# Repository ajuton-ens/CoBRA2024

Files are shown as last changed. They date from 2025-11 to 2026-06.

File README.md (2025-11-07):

# CoBRA

Le projet CoBRA (Course de Ballons Réactifs et Autonomes) à pour objectif de construire un ballon dirigeable capable de suivre un parcours de façon autonome et de larguer un colis

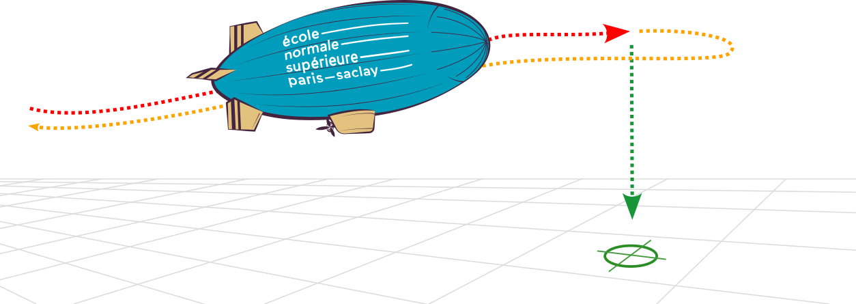
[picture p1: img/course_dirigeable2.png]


## 1 Constitution des équipes

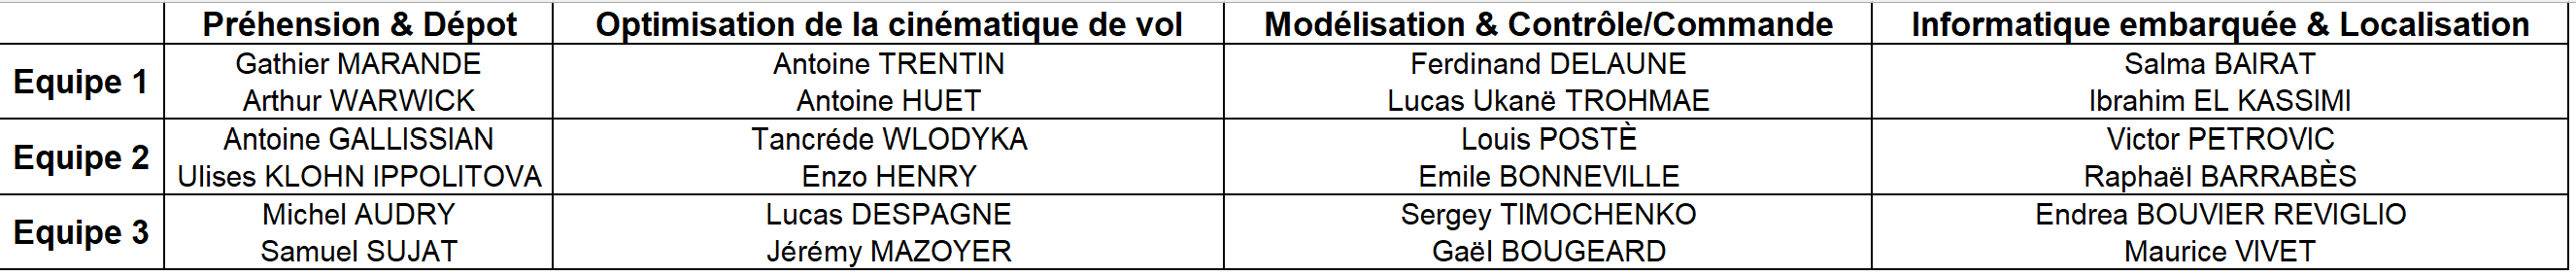
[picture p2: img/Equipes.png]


Chaque équipe doit fournir au moins 1 membre à chacun des 4 groupes de travail suivants :
* Préhension & Dépot
* Optimisation de la cinématique de vol
* Modélisation & Contrôle/Commande
* Informatique embarquée & Localisation

## 2 Analyse fonctionnelle et état de l'art
La première séance est consacrée à un travail d'étude générale du problème et d'état de l'art (projet 2023_2024 et autres dirigeables blimp).
* Découper le problème en plusieurs fonctions,
* Pour chaque fonction, spécifier les performances attendues,
* Etudier les solutions retenues en 2023 et les solutions retenues pour d'autres dirigeables,
* Etablir un schéma synoptique du dirigeable.

La semaine suivante, les groupes de travail commenceront leurs études.

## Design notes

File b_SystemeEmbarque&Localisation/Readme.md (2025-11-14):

# Systèmes embarqués et Localisation

Enseignant référent : Anthony Juton

Cette page est destinée à présenter l'avancement du travail sur :

* La prise en main de la carte Raspberry Pi Zero 2 W
* L'évaluation des télémètres infrarouge (Capteur de Distance LIDAR 8m TF-Luna)
* L'amélioration des bibliothèque d'utilisation des capteurs (BNO055, télémètre) et actionneurs (variateurs ESC et servo-moteurs)
* L'évaluation des capteurs Bosch proprioceptifs
* La localisation

## Avancement 2025-2026

**Vision**
07/11 : tests sur une nouvelle caméra des méthodes de calibration et détection des Apriltags réussis. Familiarisation avec le code de localisation utilisé actuellement sur le dirigeable. Codage sur une nouvelle camera pour la detection du centre du nouveau tag issu de la bibliothèque Aruco pour détecter le dirigeable depuis le plafond, même lorsqu'il est loin. Ceci sert pour détecter la translation du dirigeable. Pour plus tard : finalisation de ce codage pour détecter les rotations.
14/11 : Accès au stream vidéo. Début des analyses d'espacement des Apriltags.

**GPS Indoor**
GPS Indoor sous Dashboard

Tuto vidéo : https://youtu.be/Uj2_BGS1AjI 

Matériel :
- logiciel Dashboard  
-set marvelmind robotics super-MP-3D (5 beacon et un modem)

Protocole : 
1)	Installer Dashboard sur https://marvelmind.com/download/#SW ainsi que les driver nécessaire
2)	Allumer 2=ON 
3)	Connecter beacon sur le pc en filaire 
4)	Upgrade le firmware de chaque balise et du modem en haut à gauche de l’écran
5)	Cliquer sur le bouton default pour chaque beacon en bas à droite de l’écran
6)	Définir une adresse différence pour chaque beacon (ex : 1,2,3,4,5) et cliquer sur write change en haut à droite de l’écran
7)	Identifier chaque balise en mobile (Mobile Beacon a.k.a. “Hedgehog” ) ou fixe (Stationary Beacon) avec le hedgedog mode en enable ou disable . 
8)	Faire de même pour le modem (firmware+default button)
9)	Placer les balises en mesurant les distances qui les sépares et leurs altitudes respectives. 
10)	Personnellement les balises sont placées à la même hauteur (0.75 m du sol )et forme une surface rectangulaire de 3,5x5,18 m2 (voir carte associé)
11)	Créer une submap
12)	Réveiller chaque balise fixe dans la submap 0 
13)	Rentré manuellement leur position relative(x,y,z) car le mode placement auto n’est pas précis( clique droit sur le beacon sur la carte)
14)	freezsubmap 
15)	Réveiller balise mobile et fixer son altitude

=>On peut maintenant se déplacer dans l’espace (voir vidéo test)  

Piste d’amélioration :
 -placer les balises en hauteur orienté vers la zone à couvrir pour augmenter la zone et réduire les interférences du au passage des humains dans l’espace 
 
-l’altitude ne marche pas (à régler)

-position peu précise(plusieurs frezze de position) ( parfois la balise disparait) 
=>peu fiable et robuste pour le moment 
=> plus fiable/robuste avec 2 balise comme sur la vidéo tuto 

-faire un essai/test sur dirigeable en mouvement 

-intérêt pour le projet final ? 

**Proprioception**
07/11 : test du capteur BMI088, les données sont reçues via un arduino intermédiaire prochaine séance: voire à enlever l'arduino et recevoir les données directement sur le PI via I2C

## Bibliographie

[1] R. Fedorenko et V. Krukhmalev, « Indoor Autonomous Airship Control and Navigation System », MATEC Web of Conferences, vol. 42, p. 01006, 2016, doi: 10.1051/matecconf/20164201006 (http://www.matec-conferences.org/10.1051/matecconf/20164201006)

[2] J. Rao, Z. Gong, J. Luo, et S. Xie, « A flight control and navigation system of a small size unmanned airship », in IEEE International Conference Mechatronics and Automation, 2005, juill. 2005, p. 1491-1496 Vol. 3. doi: 10.1109/ICMA.2005.1626776. Disponible sur: https://ieeexplore.ieee.org/document/1626776

[3] Le site web des centrales inertielles de bosch : https://www.bosch-sensortec.com/products/motion-sensors/imus/

[8] Marvelmind propose plusieurs kits de localisation d'intérieur : https://marvelmind.com

[9] AprilTags https://april.eecs.umich.edu/software/apriltag

[10] Projet abouti https://github.com/elenagiraldo3/april_tags_autolocalization/blob/main/detect_apriltag.py

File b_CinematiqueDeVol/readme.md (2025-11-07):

# Système propulsif et directif

Enseignant référent : Bastien Durand

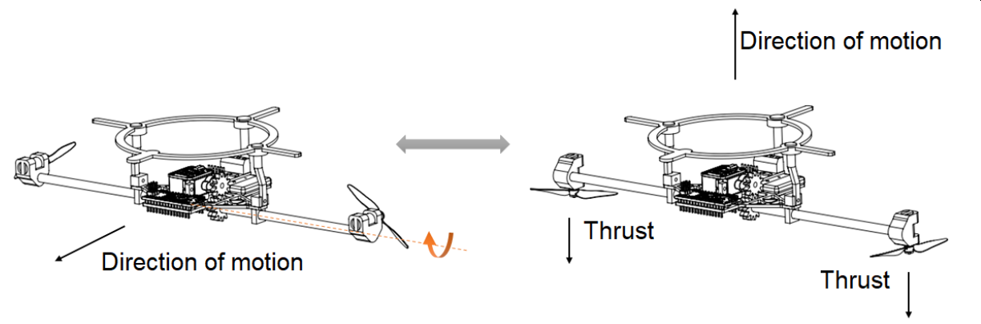
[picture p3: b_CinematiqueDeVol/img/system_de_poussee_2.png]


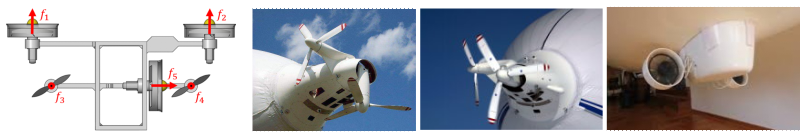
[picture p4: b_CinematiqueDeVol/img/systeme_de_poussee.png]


**Objectif** : proposer et comparer plusieurs systèmes pour déplacer et diriger le ballon (critère de comparaison, masse embarquée, consommation d'énergie, contrôlabilité, ...)

## Bibliographie

[1] J. R. H. Carvalho et al., « System Architecture of a Robotics Airship », in Proceedings of IDEAS 2019, L. Pereira, J. R. H. Carvalho, P. Krus, M. Klofsten, et V. J. De Negri, Éd., in Smart Innovation, Systems and Technologies. Cham: Springer International Publishing, 2021, p. 13‑22. doi: 10.1007/978-3-030-55374-6_2 [(paper)](./bibliographie/Carvalho et al. - 2021 - System Architecture of a Robotics Airship.pdf)

[2] F. Repoulias et E. Papadopoulos, « Dynamically feasible trajectory and open-loop control design for unmanned airships », in 2007 Mediterranean Conference on Control & Automation, juin 2007, p. 1‑6. doi: 10.1109/MED.2007.4433820. Disponible sur: https://ieeexplore.ieee.org/document/4433820

[3] S. Ul Ferdous, A. Mohammadi, et S. Lakshmanan, « Developing a low-cost autonomous blimp with a reduced number of actuators », in Unmanned Systems Technology XXI, C. M. Shoemaker, P. L. Muench, et H. G. Nguyen, Éd., Baltimore, United States: SPIE, mai 2019, p. 13. doi: 10.1117/12.2519252. Disponible sur: https://www.spiedigitallibrary.org/conference-proceedings-of-spie/11021/2519252/Developing-a-low-cost-autonomous-blimp-with-a-reduced-number/10.1117/12.2519252.full

[4] Y. Wen, L. Chen, Y. Wang, D. Sun, D. Duan, et J. Liu, « Nonlinear DOB-based explicit NMPC for station-keeping of a multi-vectored propeller airship with thrust saturation », The Aeronautical Journal, vol. 122, nᵒ 1257, p. 1753‑1774, nov. 2018, doi: 10.1017/aer.2018.91 (https://www.cambridge.org/core/journals/aeronautical-journal/article/abs/nonlinear-dobbased-explicit-nmpc-for-stationkeeping-of-a-multivectored-propeller-airship-wit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)

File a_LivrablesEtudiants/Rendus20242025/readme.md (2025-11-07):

# Info 2024/25

Pour désactiver la sortie 5 volts de la carte Raspberry pi 5

Ouvrir le fichier config.txt: sudo nano /boot/firmware/config.txt

Ajouter la igne suivante :
PSU_MAX_CURRENT=5000

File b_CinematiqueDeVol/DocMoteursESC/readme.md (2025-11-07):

# Composants

## Composants de la solution constructeur, le [Ballon de 2m de chez Aero Drum Ltd](https://www.rc-zeppelin.com/fr/int%C3%A9rieur-rc-blimps-2m.html)

| | |
| --- | --- |
|  | Moteur hélice<br />KAVAN Brushless motor [C2822-1200](https://www.kavanrc.com/en/item/kavan-brushless-motor-c2822-1200-140792)<br />Kv = 1200 rpm/V<br />Alim Lixx 2-3S<br />Diamètre axe 3.175 mm <br />Poids: 34 g|
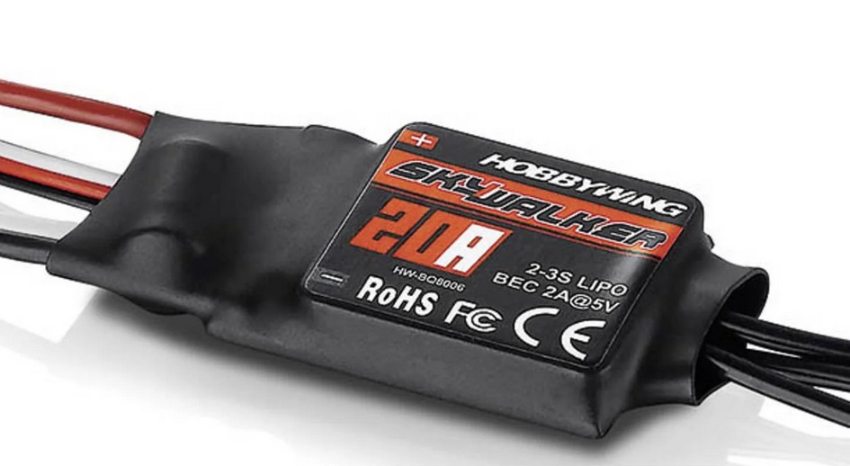
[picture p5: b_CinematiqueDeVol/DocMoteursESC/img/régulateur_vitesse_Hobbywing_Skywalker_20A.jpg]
|  | Régulateur pour moteur brushless<br />Hobbywing Skywalker 20A [Manuel](./hobbywing-skywalker-20a-regulateur-brushless-mode-demploi.pdf)<br />BEC 5V/2A<br />Alim LiPo 2-3S<br />Dimension 48x22,5 x 6 mm<br />Poids: 16,5 g|
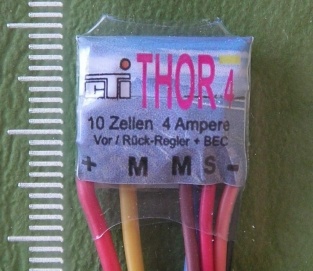
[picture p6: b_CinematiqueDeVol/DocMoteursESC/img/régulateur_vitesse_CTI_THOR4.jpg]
|  | Régulateur pour MCC deux sens de marche<br />CTI [Thor 4](https://www.cti-modellbau.de/-74-102-110-161.html) <br />Taille: 16 x 13 x 4 mmm<br />|
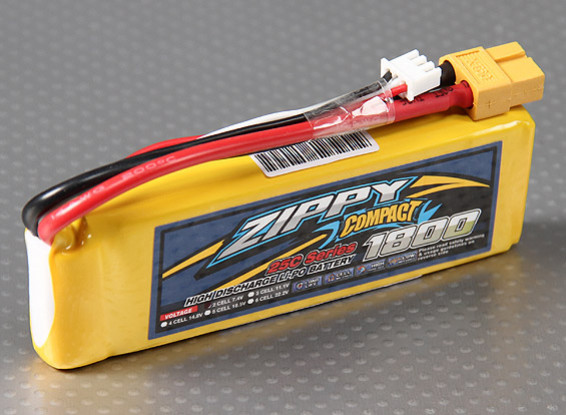
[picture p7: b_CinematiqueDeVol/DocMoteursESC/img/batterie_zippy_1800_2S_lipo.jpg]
| | Batterie<br />[Zippy compact 1800mAh 2S 25C Lipo](https://hobbyking.com/fr_fr/zippy-compact-1800mah-2s-25c-lipo-pack.html)<br />Voltage: 2S1P / 2 cellules / 7.4V<br />Poids: 110g<br />Dimensions: 105x34x16mm<br />Solde Fiche: JST-XH<br />Fiche de décharge: XT60 |
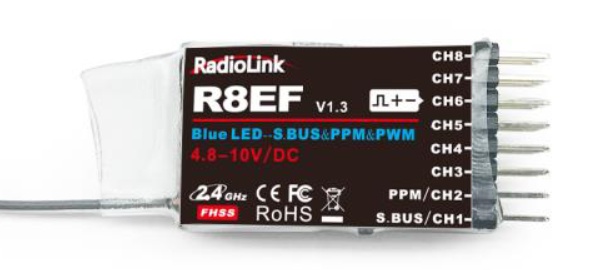
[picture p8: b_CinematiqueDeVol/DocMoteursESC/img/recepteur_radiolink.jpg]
|  | Récepteur radio<br />[Radiolink R8EF, 2.4G 8 channels receive](https://www.radiolink.com/r8ef)<br />[manuel](./Radiolink_R8EF+Introduction+Manul_2021.8.3.pdf)<br />Poids: 7g<br />Taille: 41.5 x 21.5 x 11.5mm |
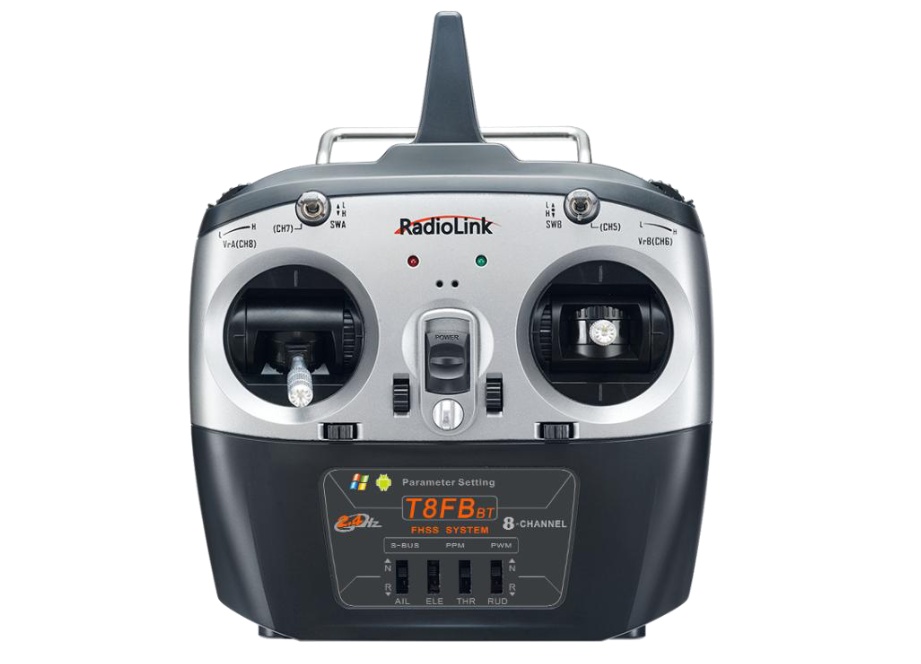
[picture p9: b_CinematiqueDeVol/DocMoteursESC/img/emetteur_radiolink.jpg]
|  | Emetteur radio<br />[Radiolink T8EF(TB), 2.4G 8 channels receive](https://www.radiolink.com/r8ef)<br />[manuel](./Radiolink_T8FB(BT)+User+Manual(with+R8EF+receiver)+2023.9.14.pdf), [Logiciels](https://www.radiolink.com/t8fb_bt_app)

## Composants pour défi 2024

| | |
| --- | --- |
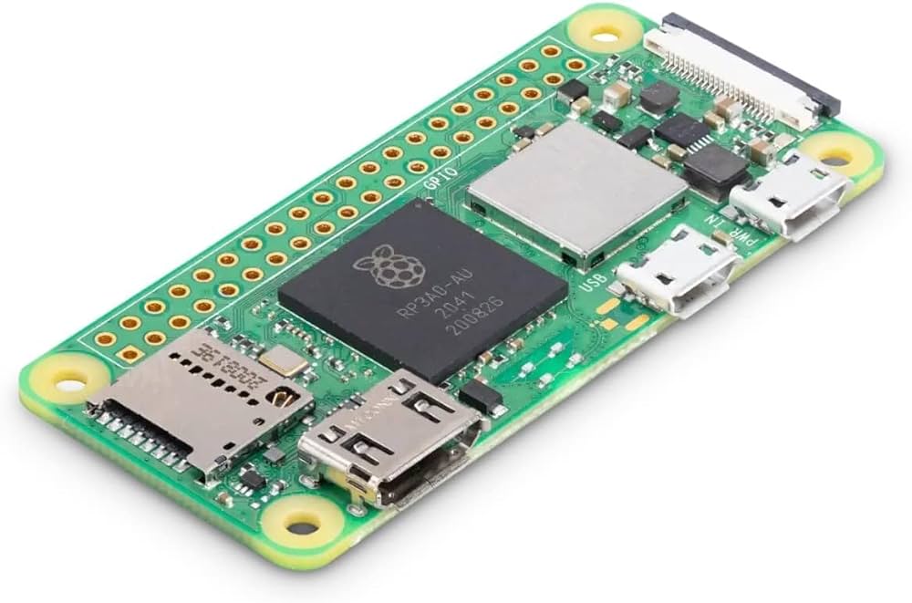
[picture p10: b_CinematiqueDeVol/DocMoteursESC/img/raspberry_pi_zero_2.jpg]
| |Contrôler - Raspberry Pi Zero 2 W<br />[schéma électrique](https://datasheets.raspberrypi.com/rpizero2/raspberry-pi-zero-2-w-reduced-schematics.pdf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..)<br />[plan mécanique](https://datasheets.raspberrypi.com/rpizero2/raspberry-pi-zero-2-w-mechanical-drawing.pdf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..)<br />[Documentation](https://www.raspberrypi.com/documentation/)|
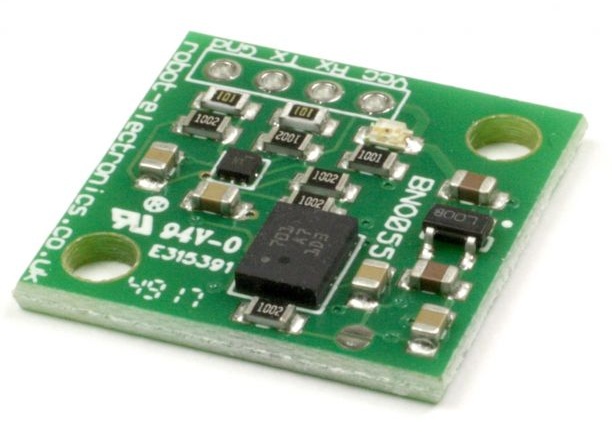
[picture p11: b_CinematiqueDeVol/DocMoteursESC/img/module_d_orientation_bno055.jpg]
|  | Module orientation absolue 9 DOF<br />[Robot electronics BNO 055](https://www.robot-electronics.co.uk/products/sensors/compass-sensors/bno055.html)<br />[Datasheet](./BNO055_datasheet.pdf), [Schéma](./BNO055_datasheet.pdf), [Layout](./BNO055_layout.pdf) BME680|
||Capteur environnemental<br />[SparkFun Environmental Sensor Breakout - BME680](https://www.sparkfun.com/products/16466) |
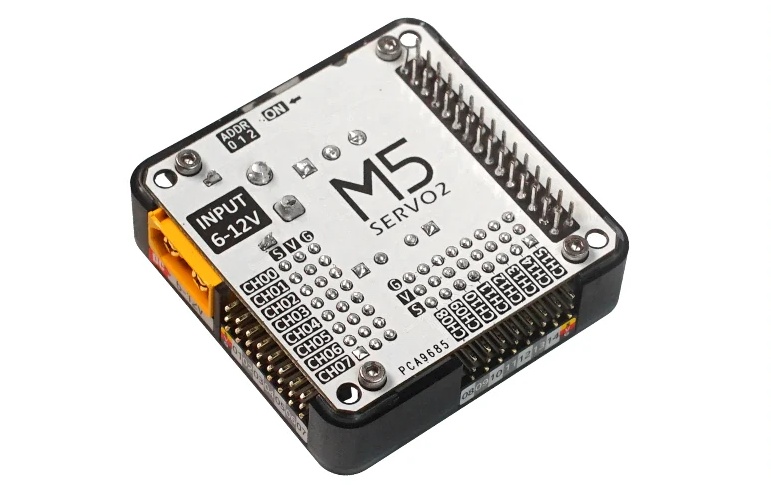
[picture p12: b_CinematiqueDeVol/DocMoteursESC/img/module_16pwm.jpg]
| | Module servo 16 canaux<br> M5Stack [ SERVO2 Module 16 Channels - 13.2 (PCA9685)](https://shop.m5stack.com/products/servo2-module-16-channels-13-2-pca9685) |
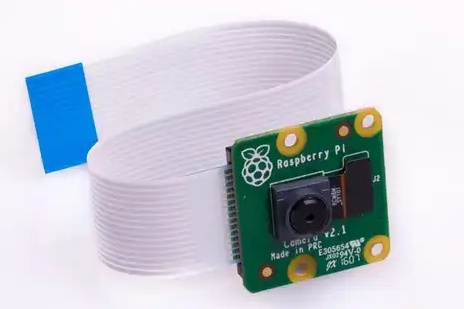
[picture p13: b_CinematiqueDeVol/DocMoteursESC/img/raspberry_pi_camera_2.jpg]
||Raspberry Pi [Camera Module 2](https://www.raspberrypi.com/products/camera-module-v2/)|
|  | Moteur brushless pour hélice<br />[Pichler Pulsar Shocky Pro 2204](https://shop.pichler.de/Brushless-Motor-PULSAR-Shocky-Pro-2204-1400-KV_1) |
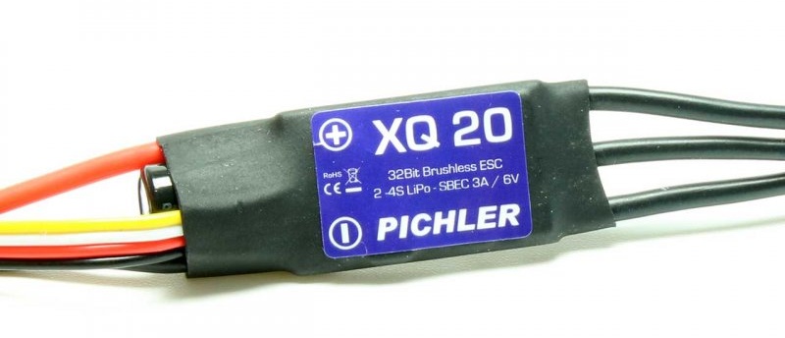
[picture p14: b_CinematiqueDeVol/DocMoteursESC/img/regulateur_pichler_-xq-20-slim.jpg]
|  | Régulateur brushless pour moteur hélice <br />[Pichler XQ+ 20 Slim](https://shop.pichler.de/Brushless-Speed-Controller-ESC-XQ-20-Slim)<br />[manuel](./pichler-xq-20-slim_manuel.pdf) |
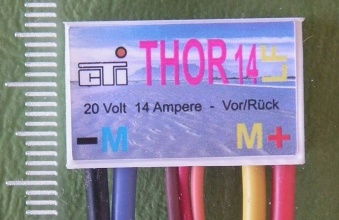
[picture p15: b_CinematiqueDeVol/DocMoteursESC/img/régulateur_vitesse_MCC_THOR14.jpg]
| | Régulateur pour MCC deux sens de marche<br />CTI [Thor 14](https://www.cti-modellbau.de/-150-151-152-166.html) |
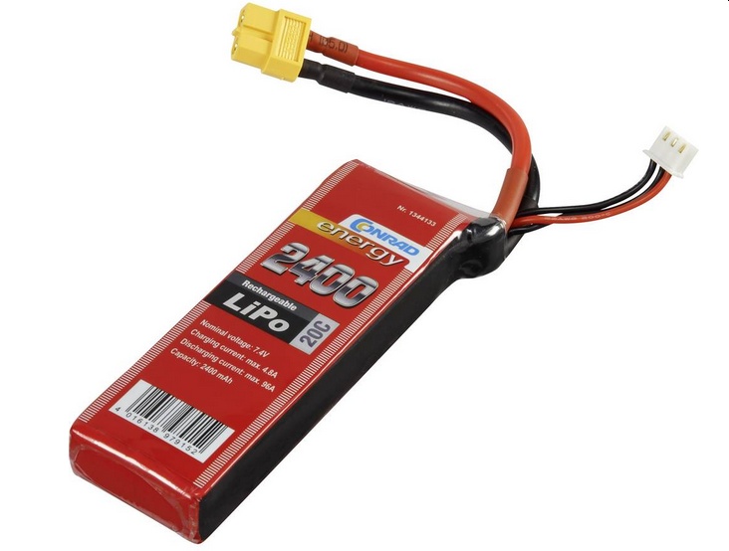
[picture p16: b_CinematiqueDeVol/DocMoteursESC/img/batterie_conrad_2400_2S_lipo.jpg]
| | Batterie<br />[Conrad 2400mAh 2S 20C Lipo](https://www.conrad.fr/fr/p/pack-de-batterie-lipo-7-4-v-2400-mah-conrad-energy-1344133-20-c-softcase-xt60-1344133.html)<br />Voltage: 2S1P / 2 cellules / 7.4V<br />Poids: 143g<br />Dimensions: 112x35x19mm<br />Connecteur: XH<br />Raccordement: XT60 |

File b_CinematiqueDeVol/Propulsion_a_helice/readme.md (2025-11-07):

# Propulsion à hélice

Enseignant référent : Bruce Anglade

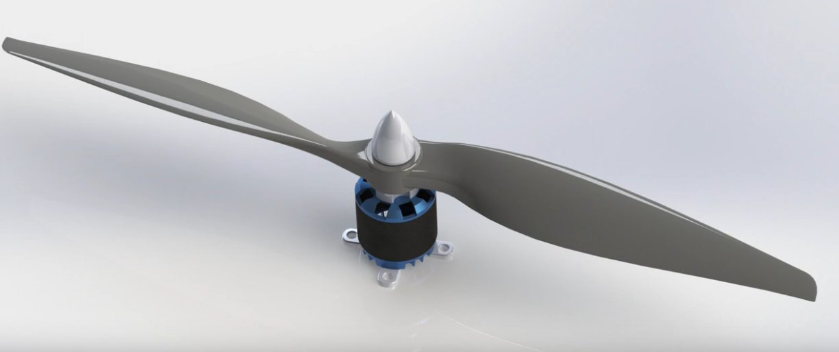
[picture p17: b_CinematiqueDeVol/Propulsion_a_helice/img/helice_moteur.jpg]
hélice + moteur


Étudiants (4) :

- Nicolas Detzen - nicolas.detzen@ens-paris-saclay.fr
- Louis Amitrano - louis.amitrano@ens-paris-saclay.fr
- Ulysse Poulain - ulysse.poulain@ens-paris-saclay.fr
- Ahmed Nachawati- ahmed.nachawati@ens-paris-saclay.fr

**objectif** : étudier la relation entre l'effort de poussée et le signal de commande, la masse totale (hélice, moteur, esc), la consommation électrique.

## Bibliographie

[1] Blimp Drone Thruster Design Overview, (23 juillet 2019). Disponible sur: https://www.youtube.com/watch?v=tUxTVcdhqJs

[2] N. Landell-Mills, Propeller thrust explained by Newtonian physics. 2021. Disponible sur: https://www.researchgate.net/publication/350604844_Propeller_thrust_explained_by_Newtonian_physics

[3] Comment savoir si son moteur et son hélice feront voler l’avion RC, (17 juillet 2022). Disponible sur: https://www.youtube.com/watch?v=99sh-BjobWw

[4] « Aircraft Propeller Theory », AeroToolbox, 24 avril 2020. Disponible sur: https://aerotoolbox.com/propeller/

[5] « Théorie de la quantité de mouvement », Wikipédia. 30 juin 2023. Disponible sur: https://fr.wikipedia.org/w/index.php?title=Th%C3%A9orie_de_la_quantit%C3%A9_de_mouvement&oldid=205599257

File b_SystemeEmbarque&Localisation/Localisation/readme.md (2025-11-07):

# Localisation d'intérieur

**Objectif** : évaluer et comparer des techniques de localisation en intérieur (ex:  radiogoniométrie Bluetooth, capteur de flux optique, fingerprinting, triangulation par vision, centrale inertielle...)

**Matériel disponible** : 
* des cartes microcontrôleurs Microbit programmables en python (avec récepteur bluetooth), des cartes microcontrôleur STM32 programmables en C, des raspberry Pi et raspberry Pi zéro (Wifi + bluetooth)
* des caméras RPI 2
* des capteurs de pression bme280
* des centrales inertielles avec Motion Processor Unit BNO055 et des centrales MPU9250
* tous les détecteurs de présence bluetooth de l'école et toutes les bornes wifi
* un kit MarvelMind Starter set Super-MP [8]

## Vision SLAM

*Mathis Goupillon* et *Guillian Audry* ont installé {Ubuntu 22.04 ; ROS2 Humble} sur une RPI4. Ils s'intéressent maintenant à la mise en oeuvre des 3 noeuds : 

* acquisition de l'image de la caméra (caméra RPI ou caméra USB)
* acquisition des données de la centrale inertielle (IMU)
* mise en oeuvre du noeud SLAM pour obtenir la carte et la position sur la carte.

Si tout fonctionne bien, il est envisageable sans trop de difficulté avec ROS2 de délocaliser le noeud SLAM sur un PC fixe, les noeuds acquisition image et IMU restant évidemment dans le contrôleur embarqué dans le dirigeable.

## Vision apriltag

*Mathieu Guerin* et *Maxime Degraeve* ont installé Raspberry OS sur une RPI zéro. L'acquisition de l'image d'une caméra USB est opérationnel. Ils ont commencé à installer apriltag pour la reconnaissance des tags (QR Code grossiers) et le calcul de leur position et orientation. Avec la position de 1 ou plusieurs tags (placés précisément dans l'atrium) dans le repère du dirigeable, on peut retrouver la position du dirigeable dans l'atrium.
L'utilisation de la smart-caméra HuskyLens est laissée de côté pour l'instant, ayant trop peu de possibilités de réglage.

## Radio

*Simon Chardin*, *Pierre-Louis Filoche* et *Pierrot Cadeilhan* ont travaillé sur le fingerprint. Après quelques essais et de la lecture biblio, la solution semble, comme on pouvait s'y attendre, peu précise (2,6 m annonce la biblio). Elle est donc abandonnée.
En attendant l'évaluation d'un système Marvelmind au retour des vacances, les étudiants ont travaillé sur micro:bit à la mise en oeuvre de télémètre ultrason SRF02 et SRF10 pour la détection d'obstacle.

## Proprioception
*Damien Chevalier* met en oeuvre sur micro:bit le capteur BME280 (température, pression, humidité) et fait une recherche de capteurs de pression plus précis. *Mathias Le Maigat* met en oeuvre la centrale inertielle (IMU) BNO055 pour estimer d'abord l'orientation du dirigeable (roll, pitch, yaw) et si possible pour estimer la position relative à la position de départ.

## Bibliographie

[1] Ellisys Bluetooth Video #14: Bluetooth Direction Finding, (8 mai 2019). Disponible sur: https://www.youtube.com/watch?v=38O2aK-aiaw

[2] R. Fedorenko et V. Krukhmalev, « Indoor Autonomous Airship Control and Navigation System », MATEC Web of Conferences, vol. 42, p. 01006, 2016, doi: 10.1051/matecconf/20164201006 (http://www.matec-conferences.org/10.1051/matecconf/20164201006)

[3] J. Rao, Z. Gong, J. Luo, et S. Xie, « A flight control and navigation system of a small size unmanned airship », in IEEE International Conference Mechatronics and Automation, 2005, juill. 2005, p. 1491-1496 Vol. 3. doi: 10.1109/ICMA.2005.1626776. Disponible sur: https://ieeexplore.ieee.org/document/1626776

[4] S. Subedi et J.-Y. Pyun, « Practical Fingerprinting Localization for Indoor Positioning System by Using Beacons », Journal of Sensors, vol. 2017, p. e9742170, déc. 2017, doi: 10.1155/2017/9742170 (https://www.hindawi.com/journals/js/2017/9742170/)

[5] X. Yu, H. Wang, et J. Wu, « A method of fingerprint indoor localization based on received signal strength difference by using compressive sensing », EURASIP Journal on Wireless Communications and Networking, vol. 2020, nᵒ 1, p. 72, avr. 2020, doi: 10.1186/s13638-020-01683-8 (https://doi.org/10.1186/s13638-020-01683-8)

[6] Angle of Arrival - Bluetooth 5.1 Direction Finding Explanation, (28 janvier 2019). Disponible sur: https://www.youtube.com/watch?v=c3XqbEKmNcM

[7] « Optical flow », Wikipedia. Disponible sur: https://en.wikipedia.org/w/index.php?title=Optical_flow&oldid=1152281324

[8] Marvelmind propose plusieurs kits de localisation d'intérieur : https://marvelmind.com

[9] AprilTags https://april.eecs.umich.edu/software/apriltag

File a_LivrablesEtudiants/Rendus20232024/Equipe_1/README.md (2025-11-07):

# Equipe n°1
## Régulateur de tension : I50115H
Droite : sortie (5V)    
Milieu : GND     
Gauche : entrée (7-36V)     
(on regarde du coté de l'étiquette-coil les pins vers le bas)

## Raspberry pi 02:
[Pinout](https://www.etechnophiles.com/rpi-zero-2w-board-layout-pinout-specs-price/)

## What i did in pip (venv/Team1) :
   
pip install adafruit-circuitpython-servokit     
pip install smbus        
pip install gpiozero        
pip install pigpio       
pip install numpy                  
pip install adafruit_bno055                  
pip install adafruit_circuitpython_bno055                  
pip install micropython_machine                  
pip install pycryptodome                  
pip install matplotlib                  

## To launch a python script in a venv:
Activate the venv : source venv/.../bin/activate         
sudo venv/.../bin/python ...py

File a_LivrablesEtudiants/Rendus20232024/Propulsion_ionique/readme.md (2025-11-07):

# Propulsion ionique

Enseignant référent : Fabien Adam

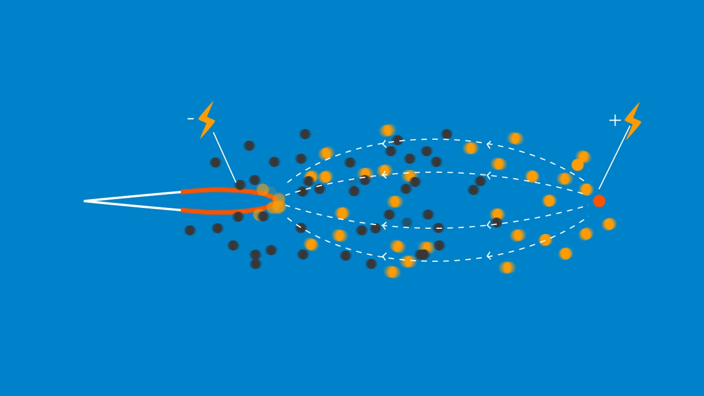
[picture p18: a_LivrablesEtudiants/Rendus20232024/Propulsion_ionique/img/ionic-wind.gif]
principe


Étudiants (4) :

- Chemsdine Ahmidach
- Melchior Personnaz
- Eliot Morard
- Samuel Dahan
- Gatien Séguy

**objectif** : élaborer un prototype et identifié l'effort de poussée obtenue en fonction du des paramètres géométriques, des matériaux et de la tension d'alimentation.

## Bibliographie

[1] S. Bernard et J.-L. Naudin, « Le projet Blimp-Lifter ». Disponible sur: http://lifterproject.online.fr/blimplifter/index.htm

[2] Ion Thruster (Side), (29 juillet 2021). Disponible sur: https://www.youtube.com/watch?v=zYVo_XjFou4

[3] Ionocraft flying, (30 août 2015). Disponible sur: https://www.youtube.com/watch?v=7nM2u2FDWsQ

[4] Electroaerodynamic Propulsion:  Is it viable?, (28 novembre 2022). Disponible sur: https://www.youtube.com/watch?v=YaLEClKGnXc

[5] C. K. Gilmore, « Electro-aerodynamic thrust for fixed-wing aircraft propulsion », Thesis, Massachusetts Institute of Technology, 2017. Disponible sur: 
https://dspace.mit.edu/handle/1721.1/112452

[6] N. Gomez-Vega, H. Xu, J. M. Abel, et S. R. H. Barrett, « Performance of decoupled electroaerodynamic thrusters », Applied Physics Letters, vol. 118, nᵒ 7, p. 074101, févr. 2021, doi: 10.1063/5.0038208

[7] Overview of MIT’s solid-state airplane, (22 novembre 2018). Disponible sur: https://www.youtube.com/watch?v=TeJyMbSSUIc

[8] J.-L. Naudin, « The Lifters Experiments ». Disponible sur: http://jnaudin.free.fr/lifters/main.htm

[9] « MIT engineers fly first-ever plane with no moving parts », MIT News | Massachusetts Institute of Technology, 21 novembre 2018. Disponible sur: https://news.mit.edu/2018/first-ionic-wind-plane-no-moving-parts-1121

[10] « Effet Biefeld-Brown », Wikipédia. 21 avril 2023. Disponible sur: https://fr.wikipedia.org/w/index.php?title=Effet_Biefeld-Brown

Ajouts des étudiants :

[11] « Force on an Asymmetric Capacitor », Thomas B. Bahder.,  Christian Fazi, ARMY RESEARCH LAB ADELPHI MD (2003), Disponible sur https://apps.dtic.mil/sti/pdfs/ADA416740.pdf

[12] Condensateur constitué par deux cylindres conducteurs: http://gerald.philippe.free.fr/files/2011/Conducteurs%20cylindriques%20en%20electrostatique.pdf
                   
[12 bis] https://claude-gimenes.fr/physique/charges-electriques/electrostatique/-iii-conducteurs-caracteristiques-principales
[13] https://arxiv.org/ftp/arxiv/papers/2002/2002.11662.pdf

[14] lien excel des mesures de la manipulation : https://ensparissaclayfr-my.sharepoint.com/:x:/g/personal/eliot_morard_ens-paris-saclay_fr/EfxHjnEue7dDnhFTeHGlXIUB3nb06A8fXRtblNC-Fcx1Bg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

[15] lien excel du planning prévisionnel : https://1drv.ms/x/s!AoqnbC4eiIVSijU25wS_YBNnT-w0

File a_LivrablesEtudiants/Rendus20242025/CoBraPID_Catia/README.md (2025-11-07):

# Remarques sur le contenu de ce dossier

Globalement, j'y ai mis les principaux fichiers nécessaires pour faire la propulsion du dirigeable. Certains manquent, comme le fichier Eagle de la carte électronique et le schéma de branchement, mais sont déjà sur le GitHub. J'ai tout modélisé sur Fusion360 donc j'ai mis les fichiers mais j'imagine que vous ne les utiliserez pas. Je n'ai mis que les fichiers aboutis, sauf le fichier principal du programme python qui fait fonctionner le dirigeable : c'est Victor qui a l'intégralité des dépendances et bibliothèques qu'il a utilisées/crées sur ROS2 sur une carte TF donc je n'ai mis que ma version de travail du programme ("main version de travail.py"). 

Vous y trouverez :

- **Le dossier "Impression"** qui contient uniquement et intégralement les fichiers stl de la structure. Quelques remarques et pistes d'amélioration :
  - "Supports moteurs bas rework.stl" est de mauvaise conception : l'hélice est trop proche de l'enveloppe et l'effet de peau fait que l'hélice aspire même en soufflant dans le bon sens. Sinon la structure est robuste et très très légère. J'ai modélisé une version améliorée mais je ne l'ai pas imprimée et donc pas testée...
  - "Supports moteurs bas.stl" est correct mais légèrement fragile selon moi et nécessiterait de mettre un cercle autour des hélices pour protéger l'utilisateur
  - "support pi cam inclinée.stl" n'a finalement pas été  utilisé puisque nous avons choisi de ne pas mettre de caméra inclinée (il était prévu d'en mettre une avec un angle de 35°)
- **Les dossiers "catia treuil AG" et "pince"** contiennent les fichiers CATIA des pièces pour la pince et le treuil. Ces pièces ont été modélisées par Ulises et Antoine Gallissian
- J'ai fourni notre poster qui contient quelques schémas et des indications utiles
- "cobra_TFLUNA_v03.py" est une version de test fonctionnelle du TFLUNA. La fonction peut être implémentée telle quelle
- "main version travail.py" : comme je disais, j'avais fait une copie du programme qui tourne pendant le fonctionnement du ballon pour travailler dessus avant d'effectuer les modifications dans le code de la raspberry (pour travailler chez moi et à cause des limites du tunnel ssh). C'est donc une version temporaire qui ne fonctionne pas forcément (je ne me souviens plus) mais qui donne 99% du fonctionnement global de la boucle 
- J'ai inclus aussi le dessin technique de la caméra raspberry utilisée (afin de la modéliser sur le fichier 3D) et la "documentation" (très incomplète et imprécise) du driver du moteur brushless.

Amusez-vous bien sur le meilleur projet de Saphire ! 😀

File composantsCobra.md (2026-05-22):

#Composants du dirigeable CoBRA

convertisseur dc-dc

Carte rasberry: PI 5

Camera : -module 3 wide (embarquée)
         -Svpro  SV-USBGS1200P01-H120 (stationnaire)

Moteurs : AS2303 F3P / 3D / 4D 2300KV 17GR T-MOTOR Intermodel 13,75 €
https://www.intermodel.fr/moteurs-electriques/12387-as2303-f3p-3d-4d-2300kv-17gr-t-motor-t-motor-brushless-moteur-3d-f3p-2300kv-4d-t-motor-as2303.html

ESC : CONTROLEUR 16A F3P 3D/4D T-MOTOR Intermodel 24,90 €
https://www.intermodel.fr/controleurs-bec/12179-controleur-16a-f3p-3d4d-t-hobby-t-motor-controleur-3d-f3p-4d-16a.html

Carte de commande :Grove PCA9685 (bus i2c vers PWM pour ESC)

Hélices : APC LP05050E 5x5E Speed 400 Electric Conrad 2,74€
https://www.conrad.fr/fr/p/apc-propeller-electrique-helice-d-avion-5-x-5-pouces-12-7-x-12-7-cm-lp05050e-2139530.html

LiDAR : TF-Luna
https://files.seeedstudio.com/wiki/Grove-TF_Mini_LiDAR/res/SJ-PM-TF-Luna-A03-Product-Manual.pdf

Accéléromètre : Grove BMI088

Capteur de pression : Adafruit LPS22

magnétometre :BMM350 

batterie : https://www.conrad.fr/fr/p/reely-pack-de-batterie-lipo-7-4-v-2400-mah-nombre-de-cellules-2-20-c-softcase-xt60-2617748.html

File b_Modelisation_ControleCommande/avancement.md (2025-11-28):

# Avancement de la modélisation et du contrôle

En octobre, prise en main du dirigeable, essais de réglage du correcteur de l'axe z.

Bilan ?

Quels programmes sont fonctionnels ?

Novembre : 
Séance du 7 novembre

PID_eloi : stable mais non précis -> erreur de 5cm pour 2m
Première approche des April Tags : grande liste convient , vibration du moteur pour vitesse > 25 : tags non détecté
Erreur de minimum : 2 minimums détectés -> lié au calcul de position 

Essai en XY (code essai..._dg , fichier: 10:24) : commande avant : gauche positif, droit négatif
Bascule et chute en commande avant-arrière

Travail sur lacet : sens horaire : 4 moteurs en positif

Séance 14 novembre
PID :

PID_alt = PID(30, 0, 1e6, 40, 0.1, 0.00001)
PID_lacet = PID(2, 0, 1e4, 30, 0.05, 0.0001)

28 novembre :

Changement pin moteur : pin 3 -> zg et pin 6 -> zd 
test_lib v12

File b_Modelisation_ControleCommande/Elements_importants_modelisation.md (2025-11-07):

## Paramètres ballons

1. Poids : $3kg$
2. Lift capacity : $0.3kg$
3. Volume : $3m^3$
4. Diamètre : $1.5m$
5. Longueur : $2m$

## Centre de poussé + centre des masses :

- doivent être à la verticale l'un de l'autre
- centre de masse de la nacelle doit être immobile (rotation des éléments autour de C.d.G)

## Frottements fluides 

3 formes de frottement en fonction du nombre de Reynolds:
1. $R_e < 1 : \quad$  $F_f = -3 \pi\mu D\cdot V$
1. $30 < R_e < 80 : \quad$  $F_f$ prop. a $V^{1.4}$ 
1. $R_e > 1 : \quad$ $F_f = -\frac{1}{2}\cdot \rho S C_x\cdot V^2$

[Source](https://fr.wikipedia.org/wiki/Frottement_fluide)

## Application numérique 
$R_e = \rho \frac{d_{cara}}{\mu}\cdot V $

Pour de l'air à faible vitesse : $\rho = 1 kg/m^3$ et $V = 1m/s $

Table : $\mu = 2e-5$

[Diamètre caractéristique](https://www.rc-zeppelin.com/indoor-rc-blimps-2m.html) : $d_{cara} = 1.5 m$

$R_e \sim 150\ 000$

Tables

## Drag coefficient
Streamline body : $C_x = 0.04$ ??

[Tableau](https://www.engineeringtoolbox.com/drag-coefficient-d_627.html), 
[wiki](https://en.wikipedia.org/wiki/Drag_coefficient) 

A voir

## Bilan des forces 
- Poids (en G)
- Poussée d'archimède (en P)
- Propulsion (en A) 
- Force de frottements fluides (en B)
- Forces des ailettes (horizontales et verticales)

... à compléter

Source pour bilan des forces : https://www.planete-sciences.org/espace/IMG/pdf/airships.pdf

## Poids et forces des hélice/moteurs

Moteurs moyen : $4.6N$ et $110g$

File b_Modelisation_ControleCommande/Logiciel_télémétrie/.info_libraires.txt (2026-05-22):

Le fichier point d'entrée du programme est : main.py

Liste des librairies utilisées :
  - time
  - math
  - tkinter
  - json
  - threading
  - socket
  - matplotlib
  - collections

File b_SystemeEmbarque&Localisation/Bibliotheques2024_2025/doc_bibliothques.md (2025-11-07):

# documentation des bibliothèques 2025

## bibliothèque bno055

### fonction initialisation

### fonction calibration

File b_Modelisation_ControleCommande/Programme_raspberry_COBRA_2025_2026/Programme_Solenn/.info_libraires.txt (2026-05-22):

Le fichier point d'entrée du programme est : aserv_h_2025_solenn.py

Liste des librairies externes utilisées :
  librairies par défault sur python :
  - time
  - math
  - os
  - json
  - numpy
  - threading
  - socket
  
  librairies à installer :
  - smbus2
  - cv2
  - picamera2
  - apriltags
  - gpiozero

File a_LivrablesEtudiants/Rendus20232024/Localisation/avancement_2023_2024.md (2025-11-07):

# Avancement du travail sur la localisation

connexions sur Covapsy2
192.168.50.130 cobrapi4

## Ven. 13/10/2023
### SLAM: *Guillan* + *Mathis*
  - lire rapports *Thomas*/*Kévin* (ROS2)
  - expliquer ROS2
  - installer ROS2
### AprilTag: *Maxime* et *Mathieu*
  - lire AprilTag
  - imprimer tags
  - installer caméra
  - installer bibliothèque sur RPI
  (si trop lent en local on peut streamer les données)
### Bilan quantitatif de l'essai boussole: *Damien* et *Mathias*
  - récupérer le bilan quantitatif des essais boussole
  - lire les infos des capteurs BME280, BNO055
  - biblio sur les nouveaux capteurs
  - ultrasons pour la détection d'obstacles
### Fingerprint: *Simon*, *Pierre-Louis* et *Pierrot*
  - essai dans l'atrium avec 2 emetteurs (checker erreur relatives)
  - essai de mesure de puissance bluetooth et WiFi avec ESP32 (c ou micropython)
  - lire doc marvelMind

# Localisation d'intérieur

**Objectif** : évaluer et comparer des techniques de localisation en intérieur (ex:  radiogoniométrie Bluetooth, capteur de flux optique, fingerprinting, triangulation par vision, centrale inertielle...)

**Matériel disponible** : 
* des cartes microcontrôleurs Microbit programmables en python (avec récepteur bluetooth), des cartes microcontrôleur STM32 programmables en C, des raspberry Pi et raspberry Pi zéro (Wifi + bluetooth)
* des caméras RPI 2
* des capteurs de pression bme280
* des centrales inertielles avec Motion Processor Unit BNO055 et des centrales MPU9250
* tous les détecteurs de présence bluetooth de l'école et toutes les bornes wifi
* un kit MarvelMind Starter set Super-MP [8]

## Vision SLAM

*Mathis Goupillon* et *Guillian Audry* ont installé {Ubuntu 22.04 ; ROS2 Humble} sur une RPI4. Ils s'intéressent maintenant à la mise en oeuvre des 3 noeuds : 

* acquisition de l'image de la caméra (caméra RPI ou caméra USB)
* acquisition des données de la centrale inertielle (IMU)
* mise en oeuvre du noeud SLAM pour obtenir la carte et la position sur la carte.

Si tout fonctionne bien, il est envisageable sans trop de difficulté avec ROS2 de délocaliser le noeud SLAM sur un PC fixe, les noeuds acquisition image et IMU restant évidemment dans le contrôleur embarqué dans le dirigeable.

## Vision apriltag

*Mathieu Guerin* et *Maxime Degraeve* ont installé Raspberry OS sur une RPI zéro. L'acquisition de l'image d'une caméra USB est opérationnel. Ils ont commencé à installer apriltag pour la reconnaissance des tags (QR Code grossiers) et le calcul de leur position et orientation. Avec la position de 1 ou plusieurs tags (placés précisément dans l'atrium) dans le repère du dirigeable, on peut retrouver la position du dirigeable dans l'atrium.
L'utilisation de la smart-caméra HuskyLens est laissée de côté pour l'instant, ayant trop peu de possibilités de réglage.

## Radio

*Simon Chardin*, *Pierre-Louis Filoche* et *Pierrot Cadeilhan* ont travaillé sur le fingerprint. Après quelques essais et de la lecture biblio, la solution semble, comme on pouvait s'y attendre, peu précise (2,6 m annonce la biblio). Elle est donc abandonnée.
En attendant l'évaluation d'un système Marvelmind au retour des vacances, les étudiants ont travaillé sur micro:bit à la mise en oeuvre de télémètre ultrason SRF02 et SRF10 pour la détection d'obstacle.

## Proprioception
*Damien Chevalier* met en oeuvre sur micro:bit le capteur BME280 (température, pression, humidité) et fait une recherche de capteurs de pression plus précis. *Mathias Le Maigat* met en oeuvre la centrale inertielle (IMU) BNO055 pour estimer d'abord l'orientation du dirigeable (roll, pitch, yaw) et si possible pour estimer la position relative à la position de départ.

## Bibliographie

[1] Ellisys Bluetooth Video #14: Bluetooth Direction Finding, (8 mai 2019). Disponible sur: https://www.youtube.com/watch?v=38O2aK-aiaw

[2] R. Fedorenko et V. Krukhmalev, « Indoor Autonomous Airship Control and Navigation System », MATEC Web of Conferences, vol. 42, p. 01006, 2016, doi: 10.1051/matecconf/20164201006 (http://www.matec-conferences.org/10.1051/matecconf/20164201006)

[3] J. Rao, Z. Gong, J. Luo, et S. Xie, « A flight control and navigation system of a small size unmanned airship », in IEEE International Conference Mechatronics and Automation, 2005, juill. 2005, p. 1491-1496 Vol. 3. doi: 10.1109/ICMA.2005.1626776. Disponible sur: https://ieeexplore.ieee.org/document/1626776

[4] S. Subedi et J.-Y. Pyun, « Practical Fingerprinting Localization for Indoor Positioning System by Using Beacons », Journal of Sensors, vol. 2017, p. e9742170, déc. 2017, doi: 10.1155/2017/9742170 (https://www.hindawi.com/journals/js/2017/9742170/)

[5] X. Yu, H. Wang, et J. Wu, « A method of fingerprint indoor localization based on received signal strength difference by using compressive sensing », EURASIP Journal on Wireless Communications and Networking, vol. 2020, nᵒ 1, p. 72, avr. 2020, doi: 10.1186/s13638-020-01683-8 (https://doi.org/10.1186/s13638-020-01683-8)

[6] Angle of Arrival - Bluetooth 5.1 Direction Finding Explanation, (28 janvier 2019). Disponible sur: https://www.youtube.com/watch?v=c3XqbEKmNcM

[7] « Optical flow », Wikipedia. Disponible sur: https://en.wikipedia.org/w/index.php?title=Optical_flow&oldid=1152281324

[8] Marvelmind propose plusieurs kits de localisation d'intérieur : https://marvelmind.com

[9] AprilTags https://april.eecs.umich.edu/software/apriltag

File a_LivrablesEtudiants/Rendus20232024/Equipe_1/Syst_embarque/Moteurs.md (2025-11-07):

# Documentation de l'équipe 1 pour l'utilisation des moteurs

## Servo-moteurs

Un servo moteur est défini par plusieurs paramètres :
- angles : `[angle_max, angle_repos, angle_min]`
- les instructions PWM associées  : `[pwm_max, pwm_repos, pwm_min]`
- le channel de connection : `int : c`

Attention : l'index  de la position `1` sur les boards est souvent le channel `0` !!

On définit plusieurs fonctions pour le servo :
#### `calculate_imp(angle)`

Permet de calculer la largeur d'impulsion à envoyer pour atteindre la position demandée. Les valeurs limites `angle_max` et `angle_min` entrées lors de la définition servent de bornes pour éviter d'abimer le servo.

#### `set_angle(angle)`

Permet d'envoyer la commande pwm au servo via le channel associé.
Une conversion liée à la bibliothèque `adafruit_servokit` est alors nécessaire.

## Moteurs brushless

Un moteur brushless est défini par plusieurs paramètres :
- les instructions PWM associées aux vitesses max et min  : `[pwm_max, pwm_min]`
- le channel de connection : `int : c`

Le moteur est commandé en vitesse entre `0` (min) et `1` (max).
Les valeurs de pwm calculées seront comprises entre 1000 µs et 2000 µs.

#### `initialisation()`

Il est nécessaire d'initialiser les ESC au démarrage. On envoit donc pendant quelques secondes une commande d'impulsion nulle (`pwm = 1000`). Le delay n'est pas placé dans cette fonction mais doit être pris en compte dans le script global.

#### `calculate_imp(speed)`

Permet de calculer la largeur d'impulsion à envoyer pour atteindre la vitesse demandée. Les valeurs limites `0` et `1`servent de bornes pour éviter d'abimer le moteur ou l'ESC.

#### `set_speed(speed)`

Permet d'envoyer la commande pwm à l'ESC via le channel associé.
Une conversion liée à la bibliothèque `adafruit_servokit` est alors nécessaire.

## Machine à courant continue

La MCC possède 2 sens de rotation et est commandée comme un moteur brushless. Il y a donc 2 plages de valeurs à définir :
- sens positif : `forward` entre `0` et `1`
- sens invers : `backward` entre `0` et `-1`

Une MCC est défini par plusieurs paramètres :
- les instructions PWM associées aux vitesses max et min  : `[pwm_max_forw, pwm_min_forw, pwm_min_back, pwm_max_back]`
- le channel de connection : `int : c`

Les plages de valeurs en pwm seront comprises entre 1000 µs et 2000 µs et une zone morte est construite dans l'ESC commandant la MCC autour de 1550 µs.

Le moteur est commandé en vitesse entre `0` (min) et `1` (max).

#### `initialisation()`

Il est nécessaire d'initialiser les ESC au démarrage. On envoit donc pendant quelques secondes une commande d'impulsion nulle (`pwm = 1550` pour la MCC). Le delay n'est pas placé dans cette fonction mais doit être pris en compte dans le script global.

#### `calculate_imp(speed)`

Permet de calculer la largeur d'impulsion à envoyer pour atteindre la vitesse demandée. Les valeurs limites `0`, `1` et `-1` servent de bornes pour éviter d'abimer le moteur ou l'ESC.

#### `set_speed(speed)`

Permet d'envoyer la commande pwm à l'ESC via le channel associé.
Une conversion liée à la bibliothèque `adafruit_servokit` est alors nécessaire.

#### `stop()`

Envoit comme consigne la valeur `pwm = 1550` pour un arrêt du moteur (zone morte de l'ESC).

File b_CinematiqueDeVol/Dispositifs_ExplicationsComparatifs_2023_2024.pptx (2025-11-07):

## CoBra

- Système propulsif et directif -

BOURDIOT Mathys
COULSON Jérémy
MPACKO PRISO Fantine
RAPAILLE Quentin
RETAILLEAU Mathieu

1/ Etablissement d’un cahier des charges
2/Propositions de dispositions de moteurs
3/ Nécessité et choix des matériaux
4/ Servomoteur
5/ Bilan

## 1/ Diagramme d’exigences

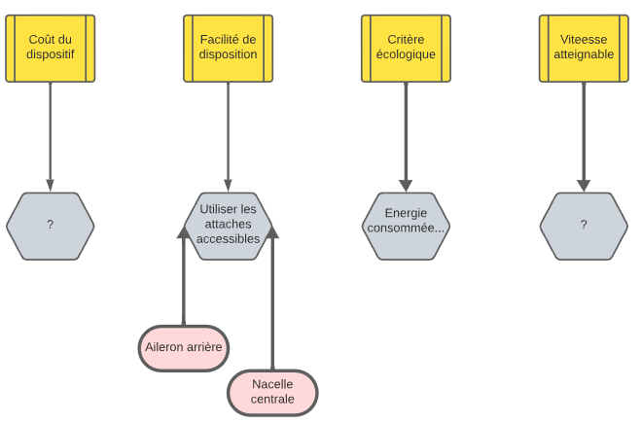
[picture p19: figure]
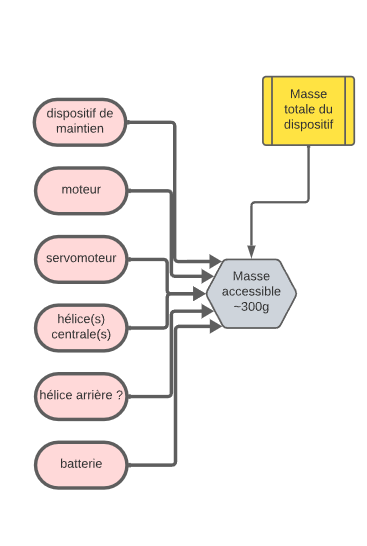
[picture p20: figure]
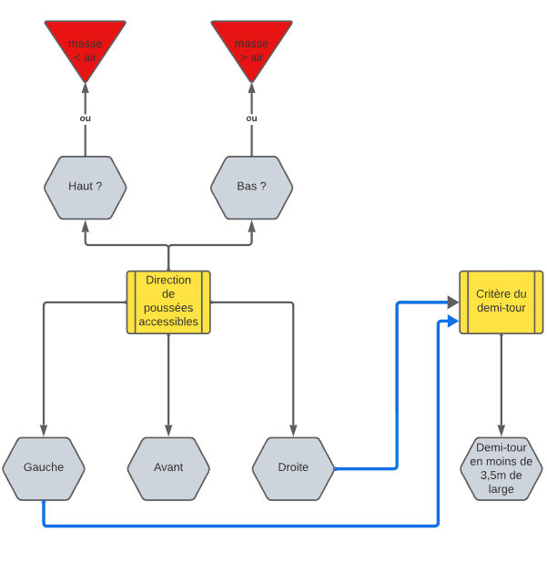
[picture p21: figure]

Ajout lien avec autre groupe et
contrainte centre de gravité ensemble
moteur sur axe de rotation

## 1/ Diagramme d’exigences

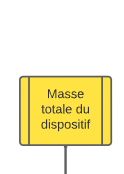
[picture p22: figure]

nombre/choix de composants

Critères prioritaires: (nécessaires)

Critères secondaires: (optimisation)

choix/disposition de composants

- Intérêt du système propulsif et directif: optimisation de ces critères

## 2/ Proposition de dispositifs

v

5 dispositions proposées

- Avantages
- Inconvénients
- Incertitudes

+ | - | ?

## -Dispositif 1-

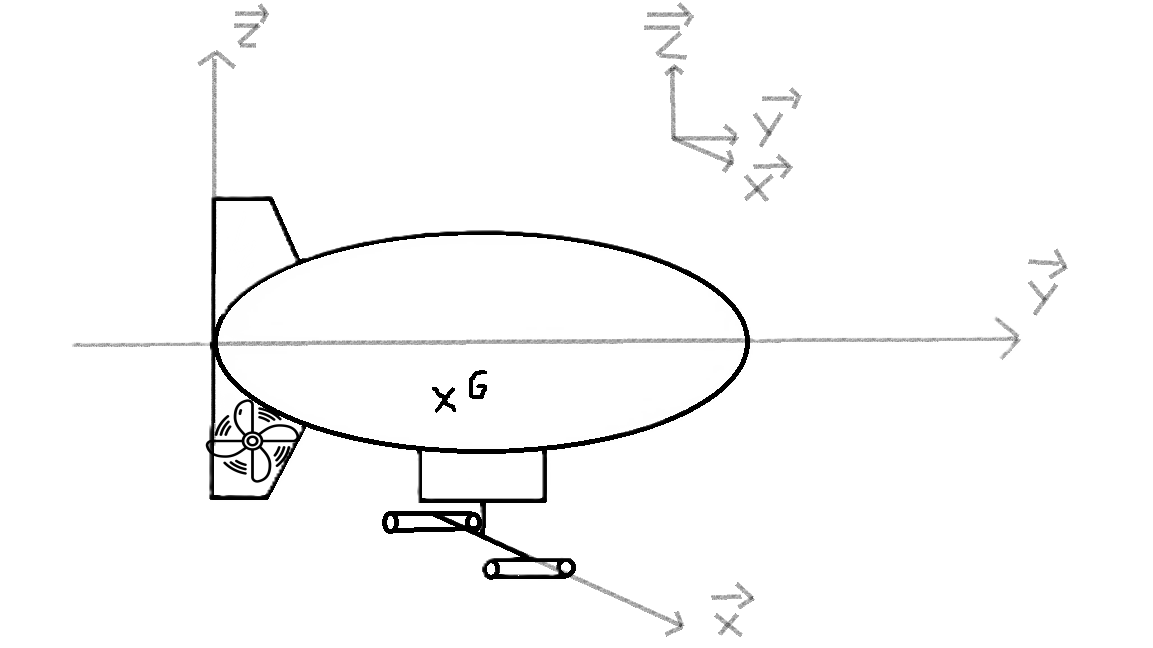
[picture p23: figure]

v

Servomoteur (rotation de l’axe moteur)

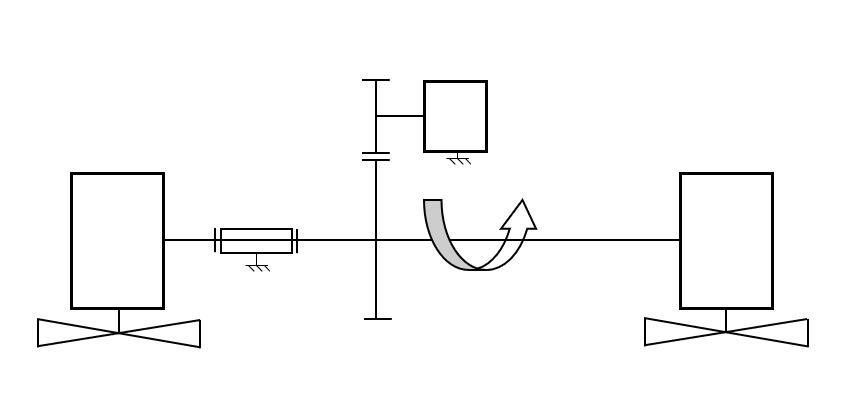
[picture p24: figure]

Moteurs (rotation des hélices)

fig2 : vue du dessus

Poussées colinéaires

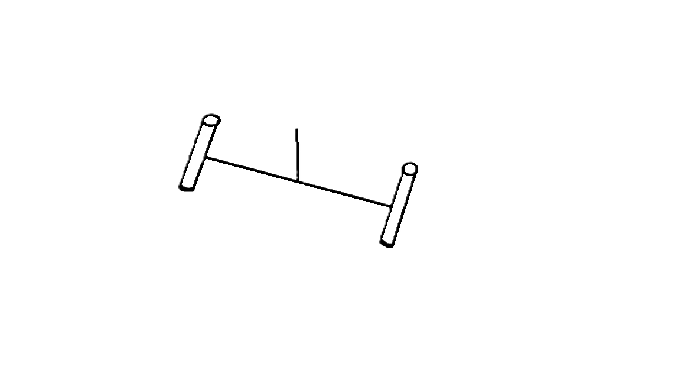
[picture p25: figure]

fig1 : vue de coté

+ | - | ?
Forte poussée sur l’axe moteur | 4 moteurs = masse/argent | Amplitude mouvement moteurs ( de -90° à 90°?)
Combiner les mobilités des moteurs | nécessité d’hélices réversibles pour marche arrière
Hélice améliore la mobilité du dirigeable | Moment sur y crée par l’hélice arrière si hors axe du barycentre

## -Dispositif 2 -

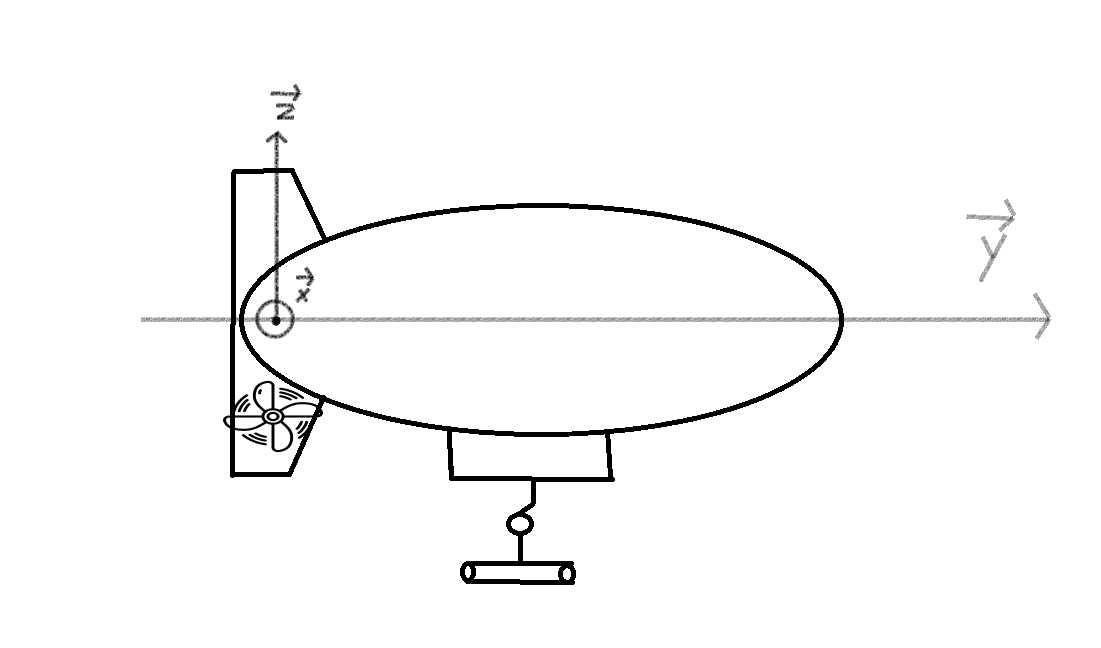
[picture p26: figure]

Servomoteur (direction axe moteur)

Moteur (rotation hélice)

Liaison pivot motorisée autour de x

+ | - | ?
Masse(prop2)<Masse(prop1) | 3 moteurs = masse /argent | Amplitude mouvement moteurs ( de -90° à 90°?)
| nécessité d’hélices réversibles pour marche arrière | Puissance du moteur nécessaire pour le moteur hélice du bas pour être équivalent aux 2 du dispositif 1
| Moment sur y de l’hélice arrière si hors axe du barycentre

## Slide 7

- Dispositif 3 -


+ | - | ?
Forte poussée sur l’axe moteur | 3 moteurs = masse/argent | Amplitude mouvement moteurs ( de -90° à 90°?)
Combiner les mobilités des moteurs | nécessité d’hélices réversibles pour marche arrière
Masse(prop2)<Masse(prop1) | Moment sur y crée par l’hélice arrière si hors axe du barycentre

## - Disposition 4 -


Servomoteur (rotation de l’axe moteur)

Moteurs (rotation des hélices)

2x dispositif ci-dessus

+ | - | ?
| 6 moteurs = masse /argent | Amplitude mouvement moteurs ( de -90° à 90°?)
| nécessité d’hélices réversibles pour marche arrière

## - Disposition 5 -


+ | - | ?
Pas de contrôle servomoteur | Maniabilité?
| nécessité d’hélices réversibles pour marche arrière

## Points avec les autres groupes

- Poids = critère à favoriser car environ 200g max : propulsion ionique à éliminer
- Composition des mouvements non nécessaire
- En attente du retour des équipes moteur et modélisation pour le choix des moteurs et leur pilotage pour choisir l’amplitude de rotation nécessaire (prévision: moteur+hélice+électronique de direction=90g)

## Dispositifs retenus


A

B

Avantages des dispositifs


C

Dispositif 1 | Dispositif 2 | Dispositif 3
Propulsion/vitesse | Masse | Pas de servomoteur à contrôler
| Dirigeabilité | Masse

## Système d’orientation des moteurs


Fig1: A


Sortie servomoteur en engrenage pour créer la rotation sur l’axe x

## Nécessité du choix des matériaux


5 pièces à imprimer

6 pièces à acheter

## Choix des matériaux d’impression


| PLA | PETG | ABS
Module d’Young [Mpa] | 2636 | 1472 | 2174
A% | 1,9 | 6,8 | 2,7
Test Charpy [J/m²] | 2,7 | 5,1 | 12,6

Source : erm-fabtest.com, polymaker (constructeur)

## Choix des matériaux achetés

Diagramme d’Ashby


## Dimensionnement axe de rotation et autres éléments en carbone


Quel diamètre choisir pour avoir une flèche acceptable ? Compromis masse/flèche

## Dimensionnement axe de rotation et autre éléments en carbone

z

flèche=(FL^3)/(3EI_z)

I_z =(πD^4)/32

Choix vis-à-vis des produits :

E_(carbone) =500GPa
F=6.37 N
flèche_(max) =0,15 mm

F avec hélice constructeur, pas la plus grande

D=7 mm

D=6,92 mm

## Servomoteur

Micro Servo FS90


+ | -
Tension d’alim | Vitesse
| Couple?
| Masse

Micro Servo GS-3005


+ | -
Masse | Couple
Vitesse
Tension d’alim


Micro Servo SG90

+ | -
Couple | Masse
Vitesse
Tension d’alim

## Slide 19

Servomoteur

Vérification du dimensionnement du servomoteur

L’accélération (angulaire) est-elle suffisante ?

Hypothèses simplificatrices :
-Pas de frottements
-Inerties engrènement et servomoteur négligeables
-On néglige les masses des câbles

Par application du théorème de l’énergie cinétique sur l’arbre en rotation :

J_(arbre) r_(arbre vers servo)^2 Ω_(servo) =C_(servo)

Ω_(servo) =(C_(servo))/(J_(arbre) r_(arbre vers servo)^2)

## SERVOMOTEUR


J_(assemblage) ≈1,213.10^(−3) Kg.m^2

J_(arbre) =J_(assemblage) +J_(moteurs)

(moteur + hélice)

Minimoida Ja niin edelleen Lupa moment d inertie d un anneau mikroaaltouuni Raha kansalais

J_(moteurs) ≈6.10^(−7) Kg.m^2

Ω_(servo) =32,4 rad.s^(−2)

## Bilan

| Modèle 1 (constru) | Modèle 2 (2 hél) | Modèle 3 (90)
Maniabilité
Stabilité
Masse | 154g | 209g | 114g
Vitesse maximale (coeff aéro = 10) | 0,7m/s | 1m/s | 0,7m/s
Facilité de fabrication | Engrenages | Engrenages & arbre central | Pas d’engrenages
Facilité de montage
Consommation électrique (20-60 W/moteur) | 2 moteurs + servo | 2 moteurs + servo | 3 moteurs
Coût | 57€ | 85€ | 56€
Impact écologique

1/5 | 2/5 | 3/5 | 4/5 | 5/5

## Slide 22

Annexe :

Impact de la variation de densité sur le module d’Young

Effects on the Mechanical Properties of the Carbon-Fiber and Polylactic Acid Specimens, Wafa Abd Soud, Ihsan A.Baqer, Mohammed Raed Ahmed

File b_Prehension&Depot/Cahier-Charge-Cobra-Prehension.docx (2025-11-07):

Cahier des charges

Concevoir, développer et réaliser un système de préhension, élévation et dépôt d'une charge.

Le système devra permettre de façon autonome, la prise et la dépose d'un colis d'une masse de 10 g (+- 1) et d'un cube de 50 mm de côté.

Le système, installé sur le dirigeable, devra autoriser le passage entre deux passerelles de l'atrium.

Le système devra disposer d'une course d'au moins 1 m.

Le système complet ne devra pas dépasser la masse de xxx g (à définir).

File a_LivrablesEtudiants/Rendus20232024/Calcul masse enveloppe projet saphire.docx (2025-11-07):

Calcul masse enveloppe

On isole le dirigeable, BAME :

-Action du poids de l’hélium

-Poussée d’Archimède

-Action du poids de l’enveloppe (inconnue)

-Action du poids de la nacelle

-Action du poids que le dirigeable peut transporter

Calcul masse nacelle

3-4 cellules lipo 3-4*20g

Moteur, ESC 100g

2 Petit servomoteur 2*9g

Plastique 54.6+10+8

Aimant : 25g

Donc mnacelle=300g

Poussée d’Archimède

ρair : 1.3 kg/m3 donc mair=1.95kg

Masse de l’hélium

mhelium : 0.25kg

Masse de la nacelle

mnacelle=300g

Masse que le dirigeable peut transporter

mbonus=200g

PFS : mhelium+menveloppe+mnacelle+mbonus –mair = 0

Donc menveloppe =1200g

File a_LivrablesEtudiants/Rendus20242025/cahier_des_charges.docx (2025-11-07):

Fonctions | Critères | Niveaux
Vitesse d’avance | Minimum | 1 m/s
Accélération | Minimum | 0,2 m/s²
Vitesse de rotation lacet | Minimum
Stabilité tangage | Maximum
Stabilité roulis | Maximum
Vitesse de monté | Minimum

COBRA CAHIER DES CHARGES 18/10/2024

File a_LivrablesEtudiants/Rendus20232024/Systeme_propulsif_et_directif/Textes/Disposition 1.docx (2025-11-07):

Disposition à hélices

Disposition 1 :


Système de direction :

Les deux moteurs du dessous sont liés par une tige, et sont donc coplanaires. Leurs poussées sont suivant le même axe. La tige maintenant les deux moteurs peut pivoter suivant l’axe x à l’aide d’un servomoteur, changeant ainsi la direction de la poussée.

De plus, une hélice à l’arrière permet de faire pivoter le dirigeable sur lui-même. Cette hélice n’a pas une forte poussée mais permet une meilleure maniabilité du dirigeable.

L’hélice arrière doit être positionnée sur le même plan que le barycentre pour éviter un moment suivant y

Ordre de grandeur de la distance entre les hélices : 20cm


Composants :

- 2 moteurs de poussée
- 1 moteur de direction
- 1 servomoteur

Avantages | Inconvénients
Assure une forte poussée suivante l’axe des deux moteurs du dessous | Il est possible que l’hélice arrière soit non nécessaire
Combiner les mobilités des moteurs | Possibilité de n’aller que vers l’avant
Barycentre sur l’axe y
Marche arrière en inclinant les moteurs

Disposition 2 :


Système de direction :

Le moteur du dessous garanti une forte poussée. Celui-ci est piloté en rotation suivant l’axe x.

De plus, une hélice à l’arrière permet de faire pivoter le dirigeable sur lui-même. Cette hélice n’a pas une forte poussée mais permet une meilleure maniabilité du dirigeable.

L’hélice arrière doit être positionnée sur le même plan que le barycentre pour éviter un moment suivant y


Avantages | Inconvénients
Gain de poids par rapport à la disposition 1 | Hélices mobiles
Stabilité autour de y | Pas de composition de mouvements
Seulement 2 hélices faciles à placer | Rotation possiblement peu efficace
Marche arrière en inclinant le moteur | Possibilité de n’aller que vers l’avant

Composants :

- 1 moteur de poussée
- 1 moteur de direction

Disposition 3 :


Système de direction :

Même disposition que la disposition 1 mais sans hélice. Les deux moteurs du dessous sont solidaires en rotation suivant x. Pour permettre une rotation suivant l’axe z, on fait tourner un moteur plus rapidement que l’autre.

Ordre de grandeur de la distance entre les hélices : 20cm

Avantages | Inconvénients
Stabilité autour de y ET de z | Pas de composition de mouvement
Vitesse plus importante | Rotation potentiellement peu efficace
Marche arrière en inclinant les moteurs

Disposition 4 :


Système de direction :

Deux paires de deux moteurs solidaires en rotation suivant x. Chaque paire peut être orientée indépendamment. De plus, en faisant varier les différentes vitesses de rotation, on peut avoir une rotation efficace.

Ordre de grandeur de la distance entre les hélices : 20cm

Avantages | Inconvénients
Stabilité autour de y ET de z | Poids plus important
Vitesse plus importante | Solution plus énergivore
Rotation efficace | Obligation de mouvement pour tourner
Marche arrière en inclinant les moteurs

Composants :

- 4moteurs
- 2 servomoteurs

Disposition 5 :

L’avantage de cette disposition est que tous les moteurs sont fixes : un à l’arrière pour pivoter, un dirigé vers l’avant pour avancer et un vers le bas pour monter / descendre.

Disposition 6 :

3 moteurs :

-1 de puissance centrale

-2 de manœuvre écartés

Problème : on impose trop de poids au système

Propulsion ionique :

Un moteur ionique est très léger, cependant pour le faire fonctionner, on a besoin d’une électronique de puissance assez lourde : il faut amplifier la tension de plusieurs piles (qq 10V) jusqu’à atteindre des milliers de volts.

Cet ensemble batterie + électronique de puissance est si lourd comparé au reste des composants qu’on peut directement en faire le centre de gravité.

Disposition 1 :

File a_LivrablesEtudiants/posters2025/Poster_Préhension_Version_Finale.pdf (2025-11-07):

# Projet pluridisciplinaire 2024-2025 Formation SAPHIRE

# Formation commune des départements de Sciences Pour l’Ingénieur

# CoBRA

### AUDRY Michel - SUJAT Samuel - MARANDE Gauthier - GALLISSIAN Antoine - WARWICK Arthur

### Pince motorisée à deux bras

Nous avons réussi à mettre en œuvre une démarche rigoureuse et collective afin de concevoir un système de préhension qui réponde au cahier des charges imposé. Une amélioration possible pour le futur serait de concevoir une pince purement mécanique qui permettrait un gain de masse considérable (pas besoin de moteur et d’électronique pour ouvrir/fermer la pince).

# Conclusion (+ Perspectives)

Dans le projet CoBRA, nous nous chargeons du système de préhension, un dispositif piloté par l’utilisateur permettant de récupérer un colis au sol, de le transporter, puis de le déposer. Notre objectif est de concevoir les parties mécaniques liées aux fonctions principales de prise et de dépose du colis.

# Les pinces

www.saphire.ens-paris-saclay.fr

# Système de préhension

Masse colis : 12,7 g ; Chargement limite du dirigeable : 650 g ; encombrement : minimum; Dimension colis : 50 mm³

Ouverture/fermeture de la pince par un MCC relié à une tige filetée (système vis-écrou). Pinces imprimées en 3D en ABS

# Les treuils

Enroulement/déroulement des fils par un arbre piloté en rotation par un MCC. Treuils imprimés en 3D en ABS avec un remplissage de 60%

Problématique d’enroulement des câbles électriques sur le tambour : utilisation d’une bague de connexion tournante (collecteur tournant)

# Résultats finaux

système
vis-écrou

Colis Colis

## Pince motorisée à trois bras

- Caractéristiques :
Matériau : ABS
Impression 3D (40% de remplissage) Masse totale : 25,1 (48,2 g treuil) g Couple moteur : 4 N.cm
Épaisseur moyenne : 2,5 mm
- Retours expérimentaux :
Levage du colis de 12,7 g
Adhérence ABS/colis
- Caractéristiques : | • Cinématique :
Impression 3D (60% de remplissage) Masse totale : 23 g
Effort de serrage nécessaire: 0,3 N Épaisseur moyenne : 2,4 mm
- Retours expérimentaux :
Levage du colis de 12,7g
Adhérence garantie ABS/colis
Vis de fixation | Vis-écrou

Support moteur
Bras-X2

Tirant-X4

Support central

Tige filetée M3 | Moteur 6V/100rpm/39,2 Nmm | Tambour
| | fils

Arbre moteur

Moteur

L’arbre du moteur est
encastré | dans | le
tambour, celui-ci est
guidé en rotation par le
support | (bâti) | et
permet d’enrouler les
fils supportant la pince.
- Équipe 1 : Tambour : Ø10mm
- Équipe 2 :

Moteur
Tambour : Ø18mm

Emplacement moteur

- Équipe 3 : | Tambour : Ø15mm
Fils | Collecteur

Vue en coupe

Insert fileté

Bâti
Moteur 6V/100rpm/78Nmm

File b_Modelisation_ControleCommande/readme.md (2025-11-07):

# Modélisation et contrôle/commande

## Modélisation dynamique

Modèle dynamique

**objectif** : établir un modèle de la dynamique du ballon (toutes les hypothèses ajoutées devront être étayées). Les nombreux paramètres du modèle devront être évalués (par mesure, par identification, ...). Identifier les paramètres de ce modèle via des essais.

## Contrôle/commande

A partir du modèle et de ses paramètres, concevoir un correcteur en simulation, tester et régler ce correcteur sur le système réel.
Dans un premier temps, on isole l'asservissement des 4 axes. Dans un second temps, on travaille sur un asservissement multivariables.

## Bibliographie

[1] M. Z. Ashraf et M. A. Choudhry, « Dynamic modeling of the airship with Matlab using geometrical aerodynamic parameters », Aerospace Science and Technology, vol. 25, nᵒ 1, p. 56‑64, mars 2013, doi: 10.1016/j.ast.2011.08.014 (./bibliographie/Ashraf and Choudhry - 2013 - Dynamic modeling of the airship with Matlab using .pdf)

[2] Chaâbani Saïd, « Dynamique non-linéaire d’un dirigeable flexible », Université d’Evry Val d’Essonne, 2014. Disponible sur: http://www.theses.fr/2014EVRY0008/document

[3] M. Khamlia, « Contribution à la modélisation et la commande des dirigeables gros porteurs non-conventionnels », phdthesis, Université Paris Saclay ; Université d’Evry-Val-d’Essonne ; Ecole Polytechnique de Tunis, 2018. Disponible sur: [https://hal.science/tel-02095871](https://hal.science/tel-02095871)

[4] R. Kukillaya et A. Pashilkar, Simulink model development, validation and analysis of high altitude airship. 2017. doi: 10.13140/RG.2.2.11844.22400 (./bibliographie/Kukillaya and Pashilkar - 2017 - Simulink model development, validation and analysi.pdf)

[5] Y. Li, M. Nahon, et I. Sharf, « Airship dynamics modeling: A literature review », Progress in Aerospace Sciences, vol. 47, nᵒ 3, p. 217‑239, avr. 2011, doi: 10.1016/j.paerosci.2010.10.001 (https://www.sciencedirect.com/science/article/pii/S0376042110000618)

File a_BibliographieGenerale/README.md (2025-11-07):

Lien vers une course de dirigeables : 
https://www.windreiter.com

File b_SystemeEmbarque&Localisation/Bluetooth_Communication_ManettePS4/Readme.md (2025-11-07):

# Bluetooth
## Appairage de la manette de PS4
- Utiliser l'icône bluetooth sur la PI pour voir les appareils bluetooth. Pour connecter la manette il faut maintenir appuyés le bouton PS et le bouton share de la manette. La manette est en mode appairage si elle clignotte de cette manière : .. .. ..

## Bibliothèque Python
- La bibliothèque à installer est pyPS4Controller. Pour l'installer écrire dans la console de commande:
  ```pip install pyPS4Controller```
- Pour utiliser l'exemple donné par la bibliothèque :
  ```https://pypi.org/project/pyPS4Controller/1.1.1/```
- L'exemple est inutilisable tel quel, il faut changer la dernière ligne par :
  ```MyController(interface="/dev/input/js0", connecting_using_ds4drv=False).listen()```
- Il suffit de modifier les instructions présentes dans les fonctions de la classe MyController afin que celles-ci soient exécutées au moment où l'action décrite est réalisée (ex: augmenter la vitesse des moteurs lorsque la gachette gauche est appuyée)

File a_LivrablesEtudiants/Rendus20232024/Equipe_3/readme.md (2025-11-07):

# 24/05/2024
## Caractérisation des moteurs
### Protocole expérimental
WhatsApp Image 2024-05-24 à 12 20 04_9289effe
On relève la force de poussée pour différentes largeurs d'impulsions imposées.
/!\ Les mesures sont faites en statique -> peut être que le comportement dynamique diffèrera un peu
### Moteur pour la poussée horizontale

WhatsApp Image 2024-05-24 à 12 17 27_020dbe35
On peut modéliser le moteur par un gain sans trop d'erreurs.
### Moteur pour la poussée verticale


Le moteur a brûlé pour une impulsion de 2000 µs. Il en a été recommandé un nouveau. Cela doit être dû à un couple trop important, qui peut venir du dimensionnement de l'hélice ou d'un frottement.
## Inventaire des masses embarquées

## Asservissement
Asservissement en vitesse pour la chaîne de propulsion horizontale.
Asservissement en position pour la chaîne de propulsion verticale.
Asservissement en position angulaire pour la chaîne de propulsion du lacet.

## Stratégies de contrôle
METTRE DES SCHEMAS
### Stratégie naïve 1
Polaire
### Stratégie naïve 2
Différence angulaire
### Autre solution
Polaire avec correction par symétrie

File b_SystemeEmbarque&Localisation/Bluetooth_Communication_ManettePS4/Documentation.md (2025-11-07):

# INTERFACE DE PILOTAGE: le controlleur Dualshock4
## Présentation:
Cette documentation vous guidera à travers l'implémentation dans python du controlleur Dualshock4 comme périphérique d'entrée.
- On utilisera une carte Rapsberry Pi Zero Wireless sous [Raspbian](https://www.raspberrypi.com/software/)
- La bibliothèque [pyPS4Controller](https://pypi.org/project/pyPS4Controller/)

## Préparation du materiel
- Il convient d'abord d'installer une configuration adéquate sur la Pi Zero. Pour ce faire, se réferer au [tutoriel](Installation_RaspberryPi4_minimum.pdf) fourni par Anthony Juton.
- Il faut appairer le controlleur Dualshock4 à la Pi Zero dans les paramètres bluetooth, via l'interface graphique RealVNC.

## Bibliothèque pyPS4Controller
- Il faut installer dans un premier lieu la bibliothèque à l'aide de la commande ```pip install pyPS4Controller```
- On peut ensuite adapter l'[exemple complet](https://pypi.org/project/pyPS4Controller/1.1.1/) fourni dans la documentation de la bibliothèque.
- /!\ L'exemple tel quel n'est pas exploitable, car le mapping par défaut des entrées n'est pas bon. Il faut donc changer la dernière ligne de l'exemple par ```MyController(interface="/dev/input/js0", connecting_using_ds4drv=False).listen()```, où le parametre ```connecting_using_ds4drv``` mis à False permet d'éviter cette erreur d'identification des entrées.
- /!\ Lors de l'exécution des fonctions ```on_'event'()```, la détection des autres entrées s'interrompt. Il faut donc éviter d'exécuter des codes de commande trop long, ou utiliser du multi-threading le cas échéant.

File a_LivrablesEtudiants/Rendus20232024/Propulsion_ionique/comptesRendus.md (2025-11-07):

# Comptes rendus du groupe de travail "Propulsion ionique"

## Séance 1 - Vendredi 6 octobre 2023

La séance s'est divisée en 2 partie majeure :

1. Explication globale du projet COBRA
    - Présentation et choix du groupe de travail / recherche
3. Présentation du principe de propulsion ionique
    - Découverte de la bibliographie
    - Discussion sur les phénomènes physiques en jeux

## Séance 2 - Vendredi 13 octobre 2023

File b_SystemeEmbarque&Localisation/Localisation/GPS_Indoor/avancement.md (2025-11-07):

# Avancement:
## Angle of arrival, Angle of departure (bof bof)
- Les signaux bluetooth/WiFi ont la bonne longueur d'onde ! Mais...
- Les signaux sont trop bruités pour obtenir une mesure de déphasage de la porteuse claire [1]
- Les signaux WiFi sont modulés en Phase/Frequence donc la mesure de déphasage en serait impactée
## RSSI based localisation technique (fingerprinting, triangulation, etc) (bof bof)
- Le RSSI, pour Received Signal Strength Indicator s'exprime en dBm selon la formule RSSI = log(P/Pref) avec Pref = 1mW
- L'incertitude mesurée sur le RSSI est de 50% autour de -30dBm, on a donc /\P = ln(10)xPrefx10^(RSSI)x/\RSSI = Pxln(10)x/\RSSI, d'où /\P/P = 69.1
- De plus, la température influence le RSSI (à prendre en compte !) [2]
- Et les meilleurs résultats ne sont pas suffisant vis à vis du CDC [3]
## Ultrason (??)
- On a fait le montage une fois ahah
## Marvelmind indoor GPS (en cours)
meilleur solution so far
Premier test de prise dans l'atrium : bon résultats, bonne précisions: sur le logiciel fourni regardez le tableau des distances et pas la carte au début 
Simon : utilisation de bibli python pour avoir les résultats directement du routeur mobile sur la console python et ainsi pouvoir les traiter manuellement.
Pilou : mise en config de la pi0, OS, reso et mise en place des script python
Pierrot : algo de distances

22/12/2023
On veut quantifier la surface couverte par un kit dans l'atrium. Mesure de l'écartement maximale entre 2 balises fixes qui nous permet de garder une précision de l'ordre du décimètre.
Choix des points: (0, 0, 0), (0, 15.2, 0), (-5.14, 30.4, 0)
Python : création d'une map dynamique à l'aide des positions xyz obtenues

Pi0 :
adresse du routeur 192.168.50.1 (covapsy;covapsy$2022)
nom d'hote : tpresopierr
username : pierr
mdp : pierr2023
IP : 192.168.50.18

WIFI : 
covapsy2
covapsy$2022

Terminal : 
ping + ip : permet de verifier la bonne connexion à l'appareil
ssh pierr@192.168.50.18

detection avec une camera branché sur une raspberry pi zero 2 (id : cobra0 / mdp : cobra0)
accés par routeur covapsy (id : covapsy2 / mdp : covapsy$2022) interface admin (id : covapsy / mdp : covapsy$2022)
port pi0 : /dev/ttyAMS0
FERMER LE logiciel MarvelMind

22/03: FAIRE la map dès le début et faire la batterie de test &
sudo chmod a+rw /dev/ttyACM0 pour avoir accès au port (trouver sur https://askubuntu.com/questions/1219498/could-not-open-port-dev-ttyacm0-error-after-every-restart)

22/03 : réception des nouvelles balises. Pb avec dashboard obligé de re télécharger.
step 1 : connecter les nouvelles balises, noter leur numéro pour les placer dans la salle
step 2 : faire la map sur dashboard 

semaine suivante : création de la map en mesurant approximativement la salle : on obtient déjà une bonne précision : next step faire une équipe pour mesurer l'atrium précisement

--vol ordi + vacances => retour en arrière -- 

26/04 : réinstallation de l'environnement marvelMind et reconnexion manuelle de toutes les balises   
        réinstallation des programmes python et reconnexion ç la RPI0

-- MarvelMind guide -- @Pilou
Le kit de balise MarvelMind permet de localiser un objet en mouvement quelque soit l'environnement (en intérieur => pas de gps). Le système de positionnement fonctionne grâce aux ultrasons et les balises communiquent entre elles via des ondes radio.
Matos à disposition : 2 kit de 5 balises + 1 modem.
Attention les 2 kits ne sont pas compatibles car pas la même fréquences de communications entre les balises (ancienne et nouvelle générations).
Le kit dernière génération fonctionne sur la fréquence 915/868 MHz. Bien faire attention à cela si on rachète un autre kit mais normalement ceux en vente actuellement sont sur ces fréquences.

Fonctionnement pratique : 5 balises = 4 balises fixes et une balise mobile à placer sur l'objet dont on veut connaitre la position. N'importe laquelle des 5 balises peut être utilisées pour être la balise mobile. Le modem (6e élément de la boite permet la communication entre les balises et avec l'ordi.

Logiciel : télécharger Dashboard (https://marvelmind.com/download/#SW aller à step5) 

Mise en place : brancher le modem à l'ordi, lancer dashboard (à trouver dans tous les fichiers après avoir de zipper le truc telechargé mais ça se trouve). Le modem devrait être reconnu direct par le logiciel => penser à télécharger le driver si pas de connexion trouver (step 4 du lien de téléchargement => il faut l'executer et relancer dashboard/l'ordi). Enlever le modem et connecter toutes las balises :
https://marvelmind.com/pics/marvelmind_navigation_system_manual.pdf p88 bonne explication de comment faire. pour les allumer mettre le pztit switch le plus à l'exterieur de la balise en ON. => penser à les éteindre après utilisation pour ne pas décharger les batteries.

Pour faire de l'embarqué. 
On utilise une RPI 0 2 connectée à covapsy3 (covapsy$2022) username : pierr , name: pierr , mdp : pierr.
ping pierr.local #pour tester la connexion à la carte
ping pierr.local -4 #pour avoir l'adresse ip
ssh pierr@192.168.50.44 pour se connecter à la carte sur cmd
sudo raspi-config #une fois connect en ssh permet de enable vnc

# Sources
- [1] Anthony Juton
- [2] https://www.researchgate.net/figure/The-change-of-RSSI-according-to-temperature_fig15_51873264
- [3] https://www.researchgate.net/publication/338944361_RoboMapper_An_Automated_Signal_Mapping_Robot_for_RSSI_Fingerprinting

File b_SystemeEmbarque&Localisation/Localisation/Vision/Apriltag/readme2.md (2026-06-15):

Voici comment utiliser les codes Adam_2026. XYZ_Adam_2026.py définit la classe Localisation qui sert pour tous les calculs de position. 
Localisation_Adam.py, sert à appliquer cette classe à un exemple réel de grille préalablement fixée au sol. Différentes informations peuvent être renvoyée, 
afin d'analyser ensuite en post-traitement les résultats .

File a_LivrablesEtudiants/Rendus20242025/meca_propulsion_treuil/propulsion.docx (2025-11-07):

1. Double hélice

Ancien système surdimensionné, diamètre hélice trop grand, espacement entre hélice trop grand. Revoir le système de pivotement de la tige (engrenage trop lourd, autre solution comme vis écrou ou courroie comme sur le système constructeur), roulements à billes pas nécessaire à priori (possibilité de palier lisse ou autre système).

Avantages | Inconvénients
Deux hélices amènent de la stabilité | Les deux hélices ont la même fonction d’un point de vue avance et soulèvement, nécessité d’asservissement pour aller tout droit

2. Hélice propulsion + poussé + queue fixes

Pertinent mais hélice de queue à rapprocher pas à mettre en boue de l’aéronef forcément. Discuter du type d’hélice/turbine

3. Double hélice bis

Système double hélice latéral non orientable. plus une hélice de poussé verticale

4. Double hélice ter

Même système que précédemment avec deux hélices de poussées verticales et une hélice contrôlant le tangage (position à définir).

PROJET COBRA SYSTEME DE PROPULSION

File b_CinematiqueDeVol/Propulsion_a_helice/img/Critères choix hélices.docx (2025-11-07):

Critères choix hélices :

- Nombre de pales
- Bruit
- Pas de l’hélice
- Forme de l’hélice (toroïdales/classiques), pour faibles ou hautes vitesses
- Matériaux
- Mode de fonctionnement (rotation rapide ou lente privilégiée)
- Vibrations système (stabilité)
- Encastrement dans forme tubulaire ?

Modes de fonctionnement

- Economie énergie -> vitesse stable
- Impulsions pour faibles amplitudes de mouvement -> grande puissance
- Mixe types d’hélices

Expériences

- Nervosité en fonction du pas = faire faibles mouvements de correction
- Autres formes pour amplitude de mouvement large
- Comportement commun ? spécifique ?

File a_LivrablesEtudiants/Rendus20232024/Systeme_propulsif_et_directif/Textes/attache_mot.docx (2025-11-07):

Système d’attache des moteurs :

Objectifs :

- Réduire les vibrations des moteurs
- Garantir un bon maintien des moteurs (axial et en rotation)
- Minimiser la masse du système
- Simplicité de montage
- Fiabilité
- Bonne précision de maintien → symétrie des deux moteurs

Composition :

Cage pour le moteur + maintien flexible

Cage pour moteur + vis de pression

Cage par pincement

Cage liée par un encastrement à la nacelle (à l’aide d’une tige)

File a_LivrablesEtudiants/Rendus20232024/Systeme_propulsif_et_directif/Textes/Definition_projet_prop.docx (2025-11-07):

Moyens de fabrication :

- Impression 3d
- Emboutissage
- Découpe haute pression
- Usinage

Contraintes :

- Poids
- Stabilité
- Flexion, résistance des solutions
- Point d’ancrage
- Coût des solutions
- Autonomie

Solutions
Motorisation | Multimoteurs | | « Monomoteur »
| Avantages | Inconvénients | Avantages | Inconvénients
| Contrôle Plus de marge pour la stratégie de commande | Poids Consommation | Légèreté | Nécessite une minutie dans la commande Mouvements limités
Structure | Matériaux | | Masse volumique (g cm⁻³⁾ | Module d’Young (GPa)
| Abs | | 1,03-1,08 | 2,4-3,0
| Pla | | 1.25 | 1,36
| Fibre de carbone (imprimée) | | 1,2 | 1,35
| Fibre de carbone | | 1.8 | 300
| Aluminium | | 2,7 | 69
| Tôle | | 7.8 | 210
| Plexiglas | | 1.18 | 2,38
| Carton | | Faible | Faible
| Forme
| Plein Imprimé 3d Treillis

Quelques ordres de grandeurs :

- Masse embarquable recommandée (hors motorisation et commande) : 200 g
- Masse un moteur : environ 50 g
- Masse hélice : 5 – 10 g

Ancrage nacelle via scratchs

Définition de fonctions coûts prévue :

- Fonction qui minimise le ratio poids/volume en fonction du matériau utilisé et de ses caractéristiques pour la structure de la nacelle
- Fonction(s) qui cherche(nt) le meilleur positionnement moteur(s) en fonction des objectifs de vitesse, de maniabilité

Utilisation de diagramme d’Ashby envisagée pour choix matériau nacelle

Sources :

- Module de Young — Wikipédia (wikipedia.org) (https://fr.wikipedia.org/wiki/Module_de_Young)
- Fichiers dans dossier

13/10/2023

Définition fonction coûts modèle double moteur (+1 à l’arrière) poutre en flexion :

- Masse volumique + flèche max → relation pour tracer diagramme Ashby
- Fonction maniabilité : un moment selon Uz généré par un moteur distant de L du centre de gravité de l’aéronef.

20/10/2023

Optimiser la matière avec SolidWorks

Modèle avec double moteur orientable indépendamment

Prendre en compte propulsion ionique

Réaliser un diagramme des exigences (sysml etc..)

Penser comment comparer les modèles : graphiques poussée etc..

Réalisation de modèle SolidWorks modèle double moteur

Servomoteur, courroie engrainement

27/10/2023

Première optimisation de matière avec SolidWorks

Création d’un diagramme Sysml basique

Modèles moteurs à 90°

Création modèle mono (constructeur) sous solidworks

10/11/2023

Idée de recherche :

Dimensionnent poulies engrènements

Présenter les autres structures

Bilan carbone dans présentation

Engrènement à imprimer

Justifier choix engrènement / budget

Elw 627Z

Travail réalisé :

Reconception support moteur modèle mono

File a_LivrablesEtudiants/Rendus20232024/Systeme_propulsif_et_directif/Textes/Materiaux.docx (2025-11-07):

Matériaux :

Matériaux pour les supports des moteurs:

- Plastiques
1) PLA (imprimable en 3D)
2) Plastique pour injection
- Métaux
1) Aluminium
2) Alliage léger
- Composites
1) Résine époxy + fibre de verre

On choisit le pla comme support des moteurs car on peut tester différentes formes avant d’en choisir une de manière définitive. De

Matériaux pour les bras :

- Plastiques
1) PLA (imprimable en 3D)
2) Plastique pour injection
- Métaux
3) Aluminium
4) Alliage léger
- Composites
2) Résine époxy + fibre de verre

Notre choix tend plus vers l’aluminium

- Plus léger
- Ne se déforme pas sous l’action de la poussée des moteurs

Matériaux pour la transmission :

- Plastiques :
1) PLA
2) Autre
- Métaux :
1) ALU
2) Acier

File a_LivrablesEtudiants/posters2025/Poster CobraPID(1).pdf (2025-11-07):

# Projet pluridisciplinaire 2024-2025

# Formation SAPHIRE

## Formation commune des départements de Sciences Pour l’Ingénieur

# Défi CoBRA

Tancrède WLODYKA – Enzo HENRY – Antoine GALISSIAN – Louis POSTE – Emile BONNEVILLE – Victor PETROVIC – Raphaël BARRABES

Supports de moteur :
- Contrainte de masse : fabriquer un système léger
- Contrainte de rigidité : limiter l’impact de la dynamique des moteurs sur l’enveloppe du Blimp
- Contrainte sécuritaire : ajouter un bumper autour des hélices

Support du module central :
- Contrainte : Assembler la batterie, les caméras, la Raspberry Pi, la carte PCB et le treuil.
- Contrainte de positionnement : centrer la caméra et le treuil sur l’axe longitudinal
1. Mesure de la masse embarquable : mmax = 720 g
2. Calcul du coefficient de traînée du Blimp par tracking d’image sur un lancer manuel

Cx = − 2m

ρStfinal

(

1
V0

− 1

Vfinal

)=0,042
3. Mesure de la poussée des anciens moteurs Fpoussée = 190 gF
4. Modèle de la dynamique du Blimp
5. Commande de nouveaux moteurs brushless correctement dimensionnés
6. Commande et configuration de nouveaux variateurs inversibles

L'objectif du projet CoBRA est de faire voler en autonomie un dirigeable (blimp) sur un parcours, et qu'il soit capable d'attraper des objets à un point A et de les relâcher à un point B. L'un des enjeux principaux est de réduire la masse totale du système pour intégrer le système de préhension sans compromettre la dynamique.

## Modélisation et calculs théoriques

## Conception en CAO des supports

www.saphire.ens-paris-saclay.fr

# Équipe CobraPID

## Choix de l'architecture de la propulsion

1. Vérification de la poussée délivrable par les nouveaux moteurs
2. Deux moteurs latéraux suffisent pour avancer, et tourner sur l'axe de lacet
3. Deux moteurs horizontaux pour assurer la montée et l'axe de tangage
4. Schématisation de notre modèle et présentation à l'équipe pour validation
5. Paramétrisation des positions des moteurs sur l'enveloppe par des fonctions coûts
- Facilité du contrôle automatisé
- Contrôle de l’altitude et de l’avancée longitudinale
- Contrôle du tangage et du lacet
- Stabilité grâce au centre de gravité bas
- Vision et préhension centrés sous le blimp
- Pas de contrôle sur le roulis
- Pas de translation latérale possible
- Moteurs délocalisés : nécessitent beaucoup de câbles

Support moteurs latéraux

Support moteurs d’élévation

Support du module central

Architecture retenue

Vue de face | Vue de dessous

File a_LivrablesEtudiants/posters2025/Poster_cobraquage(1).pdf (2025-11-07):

# Projet pluridisciplinaire 2024-2025 Formation SAPHIRE

## Formation commune des départements de Sciences Pour l’Ingénieur

# CoBRA

Antoine HUET – Antoine TRENTIN – Arthur WARWICK – Gauthier MARANDE – Salma BAIRAT – Ibrahim EL KASSIMI – Ferdinand DELAUNES – Ukäne TROHMAE

Structure centrale; Préhension; Cinématique de vol; Cinq propulseurs rendant possible : - 3 translations dans l’espace - 1 rotation selon l’axe Z; Objectif : pouvoir approcher une zone; du dirigeable en direction de la cible.; Localisation; Différents capteurs pour la position : - latitude et longitude obtenues par les aprilTags - altitude mesurée en combinant les données du télémètre et de la centrale inertielle. - orientation déterminée par la centrale inertielle.; Télémètre; Centrale; Apriltag; inertielle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

La contrainte de la masse a guidé la conception de chaque sous système, mais l’hélice de poussée verticale compense le dépassement de masse totale. Par ailleurs, l’asservissement de la commande est facilité par les éléments de propulsion non orientables. Cependant, l’inertie du dirigeable dans ses différents mouvements reste une difficulté.

Face au regain d’intérêt pour la mobilité douce et sobre permise par les dirigeables, nous souhaitons en concevoir un capable de suivre un parcours de façon autonome et de déposer un colis précisément. Ce mode de déplacement implique une contrainte de minimisation de masse majeure pour chaque sous système.

www.saphire.ens-paris-saclay.fr

# Équipe Cobraquage

tout en évitant la rotation systématique

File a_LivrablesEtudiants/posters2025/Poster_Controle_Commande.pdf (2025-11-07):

# Projet pluridisciplinaire 2024-2025

# Formation SAPHIRE

## Formation commune des départements de Sciences Pour l’Ingénieur

# CoBRA

Emile BONNEVILLE – Gaël BOUGEARD – Ferdinand DELAUNE– Louis POSTE –Sergey TIMOCHENKO - Ukanë TROHMAE

Réalisation d’une carte électronique

# Résultats :

Résultats de l’ensemble du travail.
Justification du respect ou non des objectifs initiaux

Les cartes électroniques réalisées remplissent l’ensemble des fonctions attendues. Un travail d’optimisation de la taille de la carte et donc de la masse a pu être réalisé par certaines équipes. L’asservissement reste à affiner et à adapter à chaque architecture de propulsion, et la prochaine étape consiste à finaliser l’automatisation complète, notamment par la planification de trajectoires.

L’objectif est d’automatiser le pilotage du dirigeable pour récupérer puis déposer un colis. Cela a nécessité une nouvelle architecture électronique pour intégrer des capteurs supplémentaires et s’adapter aux différents systèmes de propulsion, ainsi qu’un travail sur l’asservissement en position pour atteindre précisément les zones visées.

Mise en place de plusieurs boucles d’asservissement : Angulaire et position (x,y,z)

Schéma-bloc type des différents asservissements avec :

On a Kcapt = Klidar , Kcentrale ou Ktags en fonction de la boucle d’asservissement. Le premier pour celui en hauteur, le second pour l’asservissement angulaire et le dernier pour celui en position(x,y).

# Mise en place de l’asservissement avec correcteur PID

www.saphire.ens-paris-saclay.fr

# Systèmes embarqués et commande

Exemple de simulation avec correcteur PID pour l’asservissement en hauteur

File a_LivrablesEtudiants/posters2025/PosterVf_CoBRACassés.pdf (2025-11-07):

Introduction; OBJECTIFS
• Tige sur laquelle sont montées les hélices; • Parties du support fixées sur le dirigeable • Espace interne pour la batterie; • Tiges en carbone pour fixer les cartes électroniques; télémètre; Support de la nacelle; • Support pour le système treuil + pince
Nouvelle rotation autour de l’axe y2 :; Système de cinématique de vol :; Orientation des hélices selon l’axe x : • Orientation contrôlée par servomoteur; Système de préhension; Pince Moteur à courant continue Bras articulé avec liaisons pivot; Moteur à courant continue Tambour avec 3 câbles; Treuil; Carte électronique; Compacité Réduction de masse; Extensibilité Supporte Jusqu’à 16 moteurs
Conclusion

En conclusion, nous avons réussi à concevoir des systèmes mécaniques qui minimisent la masse tout en garantissant leurs fonctionnements. La maniabilité du dirigeable a été améliorée par l’ajout d’un nouvel axe de rotation et d’hélices réversibles. Cependant, il reste à améliorer la partie commande, complexifiée par le choix de la cinématique de vol.

- Support pour la partie capteur: caméra +
- Concevoir la partie mécanique : propulsion du dirigeable + système treuil et pince
- Développer la partie numérique : électronique de commande + automatisation du trajet
- Mener à bien l’assemblage de l’ensemble des parties du dirigeable

## Projet pluridisciplinaire 2024-2025

Formation SAPHIRE
Formation commune des départements de Sciences Pour l’Ingénieur

# CoBrasCassés

## Présentation globale du dirigeable

Jérémy MAZOYER - Lucas DESPAGNE - Samuel SUJAT - Michel AUDRY -Gaël BOUGEARD - Sergey TIMOCHENKO - Andrea BOUVIER REVIGLIO - Maurice VIVET

- Rotation contrôlée par servomoteur et fils
- Amélioration de la maniabilité du dirigeable

## Nacelle à hélices avec 2 axes de rotation

- Hélices réversible pour faciliter la direction

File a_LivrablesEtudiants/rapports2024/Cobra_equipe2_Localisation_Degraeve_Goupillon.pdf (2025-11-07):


Ecole Normale Sup ´ | erieure, SAPHIRE ´

# Projet Cobra

# Localisation - Equipe 2 ´

## DEGRAEVE Maxime, GOUPILLON Mathis Encadrant : JUTON Anthony

11 juin 2024

ENS Paris-Saclay, SAPHIRE | DEGRAEVE Maxime, GOUPILLON Mathis

## Table des matières

1 Les AprilTags | 2
2 Bibliographie | 6

## 1 Les AprilTags

### 1.1 Etat de l’art ´

Nous avons choisi d’utiliser les AprilTags pour différentes raisons :
Tout d’abord, le coût de cette technologie est très faible à part l’encre et les quelques euros de la caméra utilisée il n’y a pas de coût.
De plus, l’utilisation des AprilTags pour ce qui est de la localisation du dirigeable est sans doute la solution permettant le mieux de s’adapter à un environnement quelconque. En effet, il nous suffira de replacer les AprilTags dans le nouvel environnement lorsque l’on décide de le changer.

### 1.2 Présentation des AprilTags

L’AprilTag est une technologie de marquage visuel similaire aux codes QR, utilisée principalement en robotique. Elle permet une détection et une identification précises d’objets ou de points d’intérêt dans un environnement donné. Grâce à sa capacité à être repérée facilement par des caméras et à fournir des informations de positionnement précises, l’AprilTag est devenu un outil essentiel pour la navigation autonome des robots.
Les AprilTags se présentent comme de simple QR code, il en existe différentes familles, celle que nous utiliserons se nomme tag36h11.


Figure 1 – AprilTags 36h11

### 1.3 Protocole

L’idée est de placer une caméra sur la nacelle du dirigeable, celle ci devra être pointé vers le sol afin d’avoir dans son champ de vision un maximum d’AprilTags.
Chaque AprilTag devra être associé à une position connue dans le Repère Réel, ainsi nous pourrons déduire la position de la caméra par rapport à l’origine de ce Repère Réel.


Figure 2 – Schéma du protocole

Nous avons alors dû recouvrir l’atrium d’AprilTags, en veillant à les placer minutieusement tout en relevant leurs coordonnés dans un repère que nous avons pris soin de définir.


Figure 3 – AprilTags dans l’atrium

Pour la suite de l’implémentation en python nous avons décider d’utiliser la famille de tag ”tag36h11” et de les imprimer sur des feuilles A4 de sorte à ce que les tags fassent environ 17cm de coté (cette donnée est mesurée précisément à chaque nouvelle impression d’AprilTags et est renseignée dans le code du détecteur à chaque fois).

### 1.4 Mise en place sur python

La mise en place de la détection des AprilTags sur python fut légèrement laborieuse mais après différents essais nous avons décidés de nous baser sur le module dt-apriltags de duckietown. Pour la capture d’images nous utilisons la bibliothèque picamera2 associé à une caméra ”Raspberry Pi Camera Module 2”.


Figure 4 – Raspberry Pi Camera Module 2

Dans un premier temps il nous a fallu calibrer la caméra à l’aide de cv2 pour trouver la matrice intrinsèque de cette dernière :


Figure 5 – Matrice intrinsèque de la caméra

Dans cette matrice sont présentes les données :
(
(fx,fy) : longueur focale (horizontale,verticale) en pixels (cx,cy) : position du centre optique en pixels

Le détecteur d’AprilTags est donné sous forme de classe python du module dt-apriltags et est créé une seule fois au début de l’algorithme, en renseignant quelques paramètres (que nous ne développeront pas ici) ainsi que la famille de tags utilisée. Ensuite la fonction ”detect” de l’objet Détecteur est utilisé après chaque nouvelle prise de vue pour détecter les AprilTags visibles et les analyser, c’est dans cette fonction que l’on doit préciser à chaque fois les paramètres intrinsèques de la caméra, la taille des tags ainsi que l’image.
Une image est donc prise en échelle de gris puis envoyé dans le détecteur d’AprilTags préalablement créé pour obtenir en sortie l’id de l’AprilTag ainsi que différentes valeurs mais les seules dont nous nous serviront sont ”pose R” ainsi que ”pose t” qui sont respectivement la position de l’AprilTag par rapport à la caméra dans le Repère de la caméra et la matrice d’orientation de l’AprilTag par rapport au repère de la caméra.

### 1.5 Exploitation des résultats du code

Après avoir obtenu la position des AprilTags par rapport à la caméra dans le Repère caméra (pose t) ainsi que la matrice d’orientation du Repère de l’AprilTag vers le Repère caméra noté (pose R) pour chaque AprilTags. Il nous faut déterminer la position de la caméra par rapport à l’origine du Repère Réel, pour cela il faut tout d’abord déterminer la position de la caméra par rapport à chaque ApriTags dans le repère réel ainsi :

On note pose la position de la caméra par rapport à un AprilTag dans le repère réel :

pose = −(pose R)

T
- (pose t)
Ce vecteur de position est ensuite ajouté aux coordonnées réelle de l’AprilTag par rapport au quel la caméra se repère, on a donc :
P osition = pose + positionapriltag

Cependant, nous avons remarqué expérimentalement que dans le repère choisit que les coordonnées de pose ne correspondaient pas à celle attendues nous y avons alors appliqué une matrice de rotation de la forme :

matrice =

1 | 0 | 0
0 −1 | 0
0 | 0 | −1

On obtient donc l’expression de la position de la caméra par rapport à l’origine dans le Repère réel suivante :

P osition = matrice · pose + positionapriltag Ainsi ce processus est répété pour chaque AprilTags visibles, on moyenne chaque position obtenues pour gagner un maximum en précision.
Tout ceci est enfin répété à chaque image de la caméra ce qui nous permet d’avoir environ 15 résultats de positions par seconde.

### 1.6 Résultats

Ce système est alors fonctionnel et nous permet alors d’obtenir des résultats cohérents et précis vis à vis de la position du dirigeable.
Nous avons alors pu mener différents essais nous menant à estimer une erreur de position maximale de moins de 10cm.

## 2 Bibliographie

— Librairie dt-apriltags utilisée : https://github.com/duckietown/lib-dt-apriltags

— Calibration de la caméra : https://docs.opencv.org/4.x/dc/dbb/tutorial_py_calibration.html

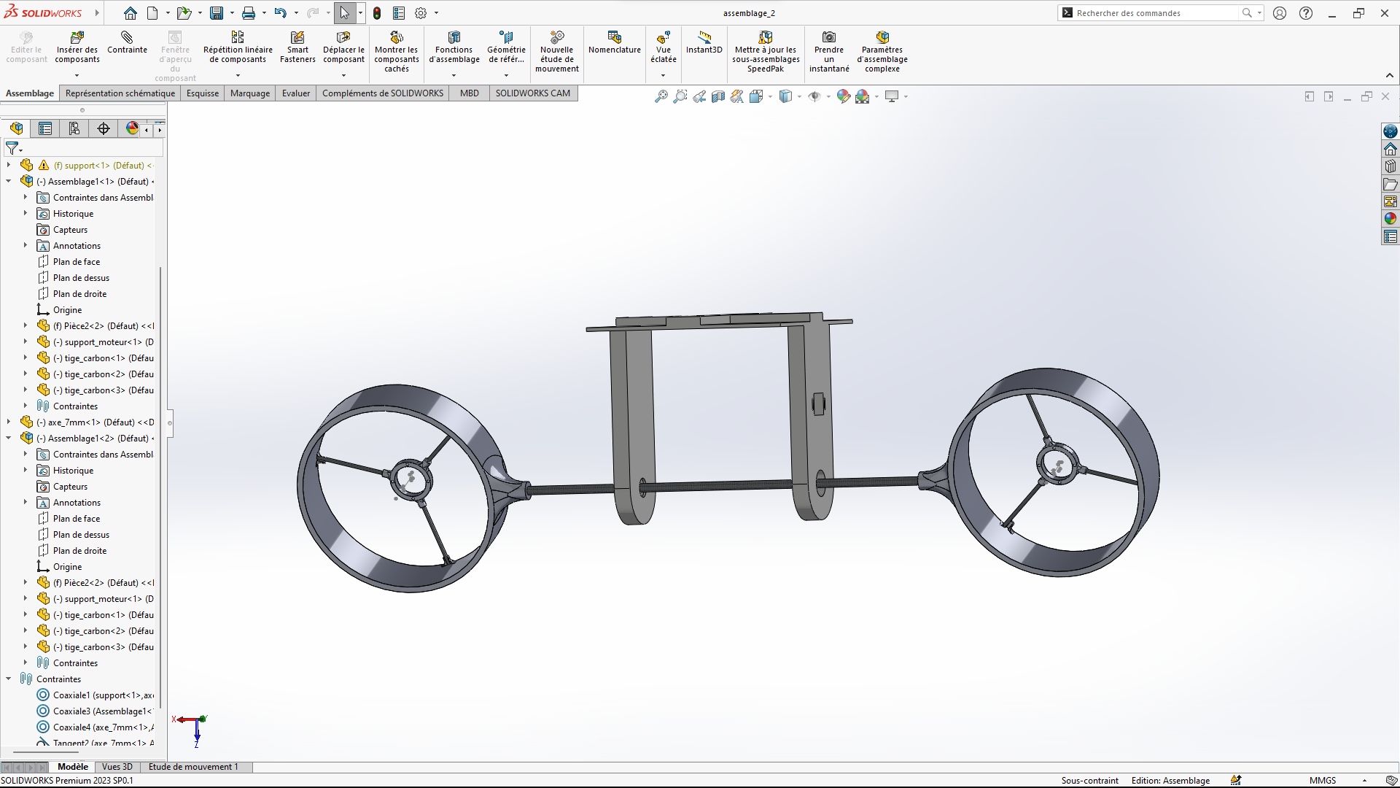
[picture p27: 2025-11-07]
a_LivrablesEtudiants/Rendus20232024/Systeme_propulsif_et_directif/Modeles_3d/Duo/Duo_1/Images/capture_2.png

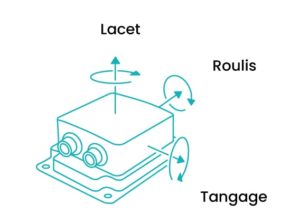
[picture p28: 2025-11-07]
b_SystemeEmbarque&Localisation/Localisation/img/centrale-inertielle-fonctionnement-cadden-300x222.jpg

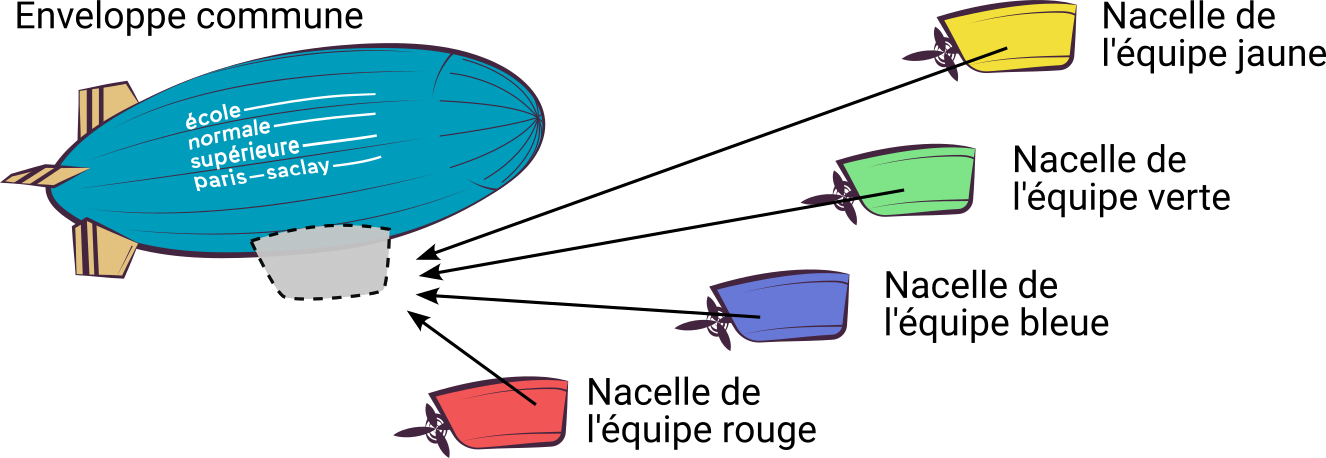
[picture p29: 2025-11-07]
img/equipes_dirigeable.png

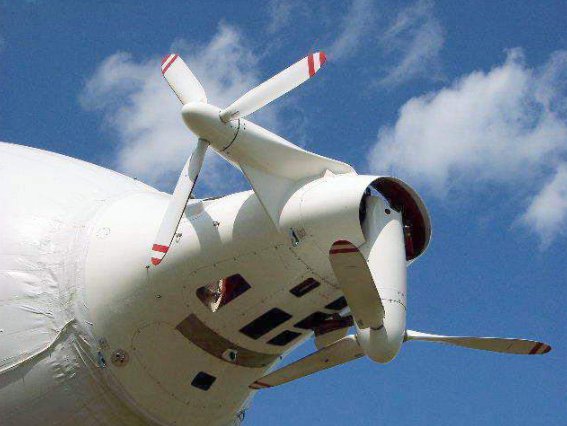
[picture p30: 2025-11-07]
b_CinematiqueDeVol/img/system_de_poussee_3.jpg

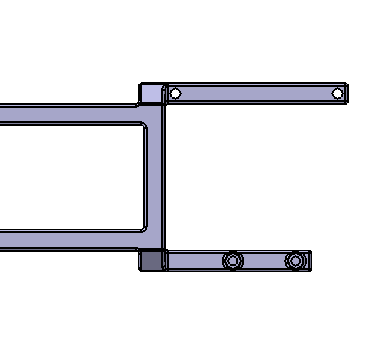
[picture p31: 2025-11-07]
a_LivrablesEtudiants/Rendus20242025/meca_propulsion_treuil/rendus/images/structurecentrale_capt.PNG

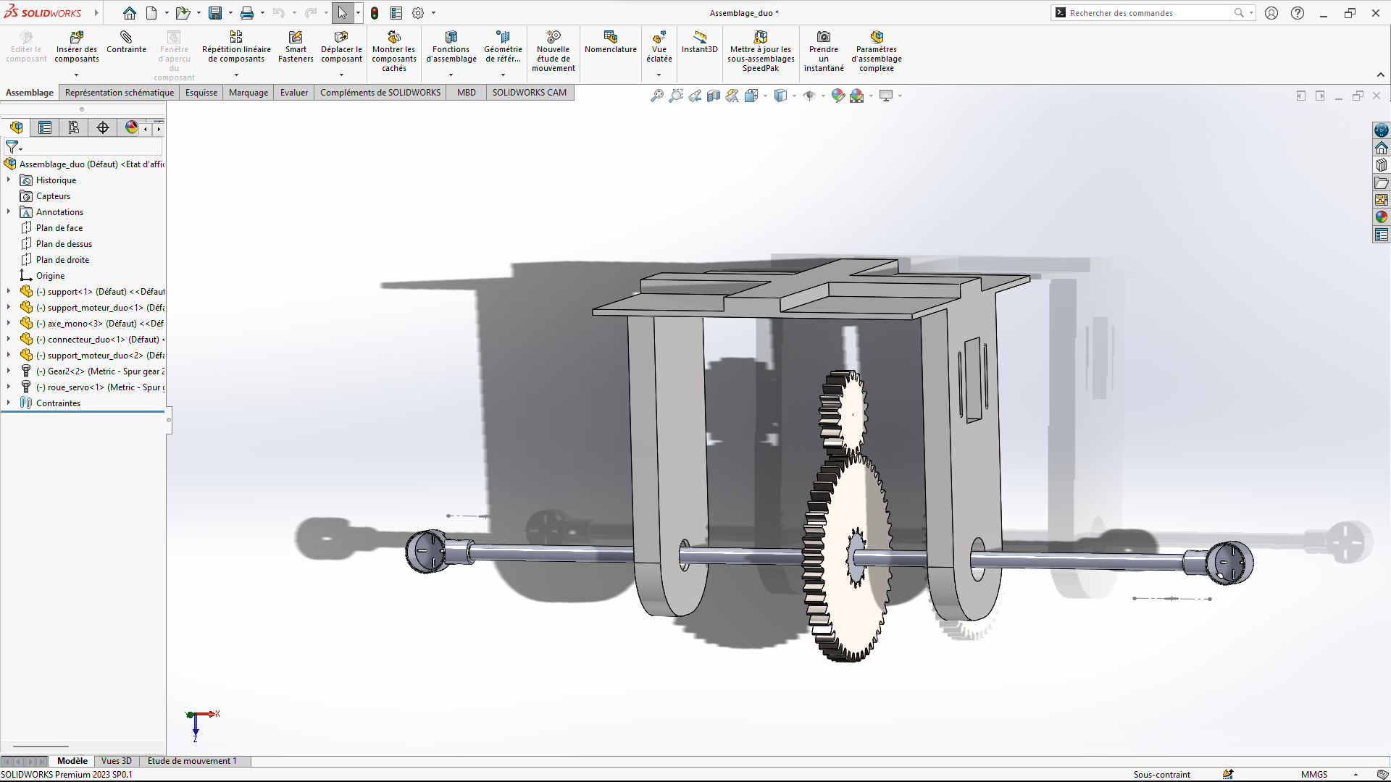
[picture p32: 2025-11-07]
a_LivrablesEtudiants/Rendus20232024/Systeme_propulsif_et_directif/Modeles_3d/Duo/Duo_1/Images/capture_duo.png

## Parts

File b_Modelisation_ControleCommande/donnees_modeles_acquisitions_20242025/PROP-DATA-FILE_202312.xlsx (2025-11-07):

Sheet: PRODUCT LIST
Product Name | Product Description | Product Code (SKU) | Categories | Price ($) | Status | Hub Diameter | Hub Thickness | Shaft Diameter | Weight | Diameter (INCHES) | Pitch (INCHES) | Color | UPC Code | Product Weight (NOT for Shipping Calculations) (LBS) | Product Weight (NOT for Shipping Calculations) (grams)
4.1x4.1E | Speed 400 Electric Use LPAR18SF or LPARM12SF adapter rings Includes one set of rings from LPAR18SF | LP04141E | Multi Rotor (Electric Only), Speed 400 (Electric Only) | 2.43 |  | 0.50 in. | 0.30 in. | 1/4 in. | 0.11 oz. | 4.1 | 4.1 | Grey | 686661040113 | 0.0069 | 3.1
4.1x4.1EP | Speed 400 Electric Pusher Reverse Rotation Use LPAR18SF or LPARM12SF adapter rings Includes one set of rings from LPAR18SF | LP04141EP | Multi Rotor (Electric Only), Speed 400 (Electric Only), Speed 400 Reverse Rotation (Left Hand Rotation) | 2.43 |  | 0.50 in. | 0.30 in. | 1/4 in. | 0.11 oz. | 4.1 | 4.1 | Grey | 686661040175 | 0.0069 | 3.1
4.2x2 | 020 Sport Use LPAR18SF or LPARM12SF adapter rings Includes one set of rings from LPAR18SF | LP04220 | Sport | 2.48 |  | 0.50 in. | 0.30 in. | 1/4 in. | 0.11 oz. | 4.2 | 2 | Grey | 686661041523 | 0.0069 | 3.1
4.2x4 | 049 Free Flight Use LPAR18SF or LPARM12SF adapter rings Includes one set of rings from LPAR18SF | LP04240 | Free Flight, Sport | 2.48 |  | 0.50 in. | 0.30 in. | 1/4 in. | 0.11 oz. | 4.2 | 4 | Grey | 686661041530 | 0.0069 | 3.1
4.4x4 | 049 Free Flight Use LPAR18SF or LPARM12SF adapter rings Includes one set of rings from LPAR18SF | LP04440 | Free Flight, Sport | 2.48 |  | 0.50 in. | 0.30 in. | 1/4 in. | 0.14 oz. | 4.4 | 4 | Grey | 686661040106 | 0.0088 | 4.0
4.5x3.5 | 1/2A Pylon / Combat Use LPAR18SF or LPARM12SF adapter rings Includes one set of rings from LPAR18SF | LP04535 | Pylon Combat, 1/2A Pylon Combat | 2.48 |  | 0.50 in. | 0.30 in. | 1/4 in. | 0.14 oz. | 4.5 | 3.5 | Grey | 686661040083 | 0.0088 | 4.0
4.5x4 | 1/2A Pylon / Combat Use LPAR18SF or LPARM12SF adapter rings Includes one set of rings from LPAR18SF | LP04540 | Pylon Combat, 1/2A Pylon Combat | 2.48 |  | 0.50 in. | 0.30 in. | 1/4 in. | 0.14 oz. | 4.5 | 4 | Grey | 686661040090 | 0.0088 | 4.0
4.5x4.1E | Speed 400 Electric Use LPAR18SF or LPARM12SF adapter rings Includes one set of rings from LPAR18SF | LP04541E | Speed 400 (Electric Only) | 2.43 |  | 0.50 in. | 0.28 in. | 1/4 in. | 0.14 oz. | 4.5 | 4.1 | Grey | 686661040076 | 0.0088 | 4.0
4.6x3 | 1/2A Pylon / Combat | LP04630 | Pylon Combat, 1/2A Pylon Combat | 2.48 |  | 0.65 in. | 0.31 in. | 3/16 in. | 0.18 oz. | 4.6 | 3 | Grey | 686661040021 | 0.0113 | 5.1
4.7x4.2E | Speed 400 Electric Use LPAR18SF or LPARM12SF adapter rings Includes one set of rings from LPAR18SF | LP04742E | Speed 400 (Electric Only) | 2.43 |  | 0.50 in. | 0.26 in. | 1/4 in. | 0.11 oz. | 4.7 | 4.2 | Grey | 686661040038 | 0.0069 | 3.1
4.75x4.5E | Speed 400 Electric Use LPAR18SF or LPARM12SF adapter rings Includes one set of rings from LPAR18SF and LPARM12SF | LP04745E | Speed 400 (Electric Only) | 2.43 |  | 0.50 in. | 0.30 in. | 1/4 in. | 0.14 oz. | 4.75 | 4.5 | Grey | 686661040120 | 0.0088 | 4.0
4.75x4.5EC | Speed 400 Electric Carbon Use LPAR18SF or LPARM12SF adapter rings Includes one set of rings from LPAR18SF and LPARM12SF Material: 40% Carbon / 60% Nylon | LP04745EC | Speed 400 (Electric Only), Carbon Fiber (Electric Only) | 7.43 |  | 0.50 in. | 0.30 in. | 1/4 in. | 0.11 oz. | 4.75 | 4.5 | Black | 686661040137 | 0.0069 | 3.1
4.75x4.75E | Speed 400 Electric Use LPAR18SF or LPARM12SF adapter rings Includes one set of rings from LPAR18SF and LPARM12SF | LP04747E | Multi Rotor (Electric Only), Speed 400 (Electric Only) | 2.43 |  | 0.50 in. | 0.30 in. | 1/4 in. | 0.14 oz. | 4.75 | 4.75 | Grey | 686661040052 | 0.0088 | 4.0
4.75x4.75EC | Speed 400 Electric Carbon Use LPAR18SF or LPARM12SF adapter rings Includes one set of rings from LPAR18SF and LPARM12SF Material: 40% Carbon / 60% Nylon | LP04747EC | Speed 400 (Electric Only), Carbon Fiber (Electric Only) | 7.43 |  | 0.50 in. | 0.30 in. | 1/4 in. | 0.11 oz. | 4.75 | 4.75 | Black | 686661040144 | 0.0069 | 3.1
4.75x4.75EP | Speed 400 Electric Pusher Reverse Rotation Use LPAR18SF or LPARM12SF adapter rings Includes one set of rings from LPAR18SF and LPARM12SF | LP04747EP | Multi Rotor (Electric Only), Speed 400 (Electric Only), Speed 400 Reverse Rotation (Left Hand Rotation) | 2.43 |  | 0.50 in. | 0.30 in. | 1/4 in. | 0.14 oz. | 4.75 | 4.75 | Grey | 686661040182 | 0.0088 | 4.0
4.75x4 | 1/2A Pylon / Combat | LP04754 | Pylon Combat, 1/2A Pylon Combat | 2.48 |  | 0.65 in. | 0.34 in. | 3/16 in. | 0.21 oz. | 4.75 | 4 | Grey | 686661040045 | 0.0131 | 5.9
4.75x5.5E | Speed 400 Electric Use LPAR18SF or LPARM12SF adapter rings Includes one set of rings from LPAR18SF and LPARM12SF | LP04755E | Speed 400 (Electric Only) | 2.43 |  | 0.50 in. | 0.30 in. | 1/4 in. | 0.14 oz. | 4.75 | 5.5 | Grey | 686661040151 | 0.0088 | 4.0
5x3 | 049 Free Flight | LP05030 | Free Flight, Sport | 2.48 |  | 0.65 in. | 0.32 in. | 3/16 in. | 0.21 oz. | 5 | 3 | Grey | 686661050013 | 0.0131 | 5.9
5x3E | Thin Electric Use LPAR18SF or LPARM12SF adapter rings Includes one set of rings from LPAR18SF and LPARM12SF | LP05030E | Thin Electric, Multi Rotor (Electric Only) | 2.43 |  | 0.50 in. | 0.23 in. | 1/4 in. | 0.11 oz. | 5 | 3 | Grey | 686661050143 | 0.0069 | 3.1
5x3EP | Thin Electric Pusher Reverse Rotation Use LPAR18SF or LPARM12SF adapter rings Includes one set of rings from LPAR18SF and LPARM12SF | LP05030EP | Thin Electric, Multi Rotor (Electric Only), Electric Reverse Rotation (Left Hand Rotation) | 2.43 |  | 0.50 in. | 0.23 in. | 1/4 in. | 0.11 oz. | 5 | 3 | Grey | 686661050150 | 0.0069 | 3.1
5x4R-LH | Reversible ESC - LH, 2 Pack 3D Reversible ESC Includes two LH rotation propellers | LP05040R-LH | Multi Rotor (Electric Only), 3D - Reversible ESC | 2.97 |  | 0.50 in. | 0.28 in. | 5 mm | 0.14 oz. | 5 | 4 | Grey | 686661050617 | 0.0176 | 8.0
5x4R-RH | Reversible ESC - RH, 2 Pack 3D Reversible ESC Includes two RH rotation propellers | LP05040R-RH | Multi Rotor (Electric Only), 3D - Reversible ESC | 2.97 |  | 0.50 in. | 0.28 in. | 5 mm | 0.14 oz. | 5 | 4 | Grey | 686661050600 | 0.0176 | 8.0
5x4.1SF | Slow Flyer Indoor 3D (SF3D) For Indoor 3D Aerobatics | LP05041SF | Indoor 3D | 2.33 |  | 0.50 in. | 0.15 in. | 5 mm | 0.08 oz. | 5 | 4.1 | Grey | 686661050860 | 0.0044 | 2.0
5x5E | Speed 400 Electric Use LPAR18SF or LPARM12SF adapter rings Includes one set of rings from LPAR18SF and LPARM12SF | LP05050E | Multi Rotor (Electric Only), FPV Racing / Freestyle, Speed 400 (Electric Only) | 2.43 |  | 0.50 in. | 0.25 in. | 1/4 in. | 0.14 oz. | 5 | 5 | Grey | 686661050020 | 0.0088 | 4.0
5x5EP | Speed 400 Electric Pusher Reverse Rotation Use LPAR18SF or LPARM12SF adapter rings Includes one set of rings from LPAR18SF and LPARM12SF | LP05050EP | Multi Rotor (Electric Only), FPV Racing / Freestyle, Speed 400 (Electric Only), Speed 400 Reverse Rotation (Left Hand Rotation) | 2.43 |  | 0.50 in. | 0.25 in. | 1/4 in. | 0.14 oz. | 5 | 5 | Grey | 686661050587 | 0.0088 | 4.0
5x5F | Folding Electric Propeller Blades Use FH35mm-6 (LPFH2-6) Hub - not included | LP05050F | Folding (Electric Only) | 3.35 |  | NA | See LPFH | See LPFH | 0.11 oz. | 5 | 5 | Grey | 686661050082 | 0.0069 | 3.1
5x5FP | Folding Electric Propeller Blades Reverse Rotation Use FH35mm-6 (LPFH2-6) Hub - not included | LP05050FP | Folding (Electric Only) | 3.35 |  | NA | See LPFH | See LPFH | 0.11 oz. | 5 | 5 | Grey | 686661050839 | 0.0069 | 3.1
5x7.5E | Speed 400 Electric Use LPAR18SF or LPARM12SF adapter rings Includes one set of rings from LPARM12SF Includes Nylon spacer for hub | LP05075E | Multi Rotor (Electric Only), FPV Racing / Freestyle, Speed 400 (Electric Only) | 2.54 |  | 0.50 in. | 0.28 in. | 5 mm | 0.18 oz. | 5 | 7.5 | Grey | 686661050808 | 0.0110 | 5.0
5x7.5EP | Speed 400 Electric Pusher Reverse Rotation Use LPAR18SF or LPARM12SF adapter rings Includes one set of rings from LPARM12SF Includes Nylon spacer for hub | LP05075EP | Multi Rotor (Electric Only), FPV Racing / Freestyle, Speed 400 (Electric Only), Speed 400 Reverse Rotation (Left Hand Rotation) | 2.54 |  | 0.50 in. | 0.28 in. | 5 mm | 0.18 oz. | 5 | 7.5 | Grey | 686661050822 | 0.0110 | 5.0
5.1x4.5E | Thin Electric Use LPAR18SF or LPARM12SF adapter rings Includes one set of rings from LPAR18SF and LPARM12SF | LP05145E | Thin Electric | 2.43 |  | 0.50 in. | 0.34 in. | 1/4 in. | 0.18 oz. | 5.1 | 4.5 | Grey | 686661050099 | 0.0113 | 5.1
5.1x5.0E-B4 | FPV Racing Bundle (5.1x5.0E and 5.1x5.0EP) Package contains four propellers (2 standard rotation and 2 reverse rotation) | LP05150E-B4 | Multi Rotor (Electric Only), Bundle (2 CW &amp; 2 CCW), FPV Racing / Freestyle | 5.36 |  | 0.50 in. | 0.28 in. | 5 mm | 0.14 oz. | 5.1 | 5 | GREY | 686661050679 | 0.0352 | 16.0
5.2x6.0E-B4 | FPV Racing Bundle (5.2x6.0E and 5.2x6.0EP) Package contains four propellers (2 standard rotation and 2 reverse rotation) | LP05260E-B4 | Multi Rotor (Electric Only), Bundle (2 CW &amp; 2 CCW), FPV Racing / Freestyle | 5.36 |  | 0.50 in. | 0.28 in. | 5 mm | 0.14 oz. | 5.2 | 6 | Grey | 686661050648 | 0.0352 | 16.0
5.25x4.75E | Speed 400 Electric Use LPAR18SF or LPARM12SF adapter rings Includes one set of rings from LPAR18SF and LPARM12SF | LP053475E | Speed 400 (Electric Only) | 2.43 |  | 0.50 in. | 0.30 in. | 1/4 in. | 0.14 oz. | 5.25 | 4.75 | Grey | 686661050075 | 0.0088 | 4.0
5.25x5.5E | Speed 400 Electric Use LPAR18SF or LPARM12SF adapter rings Includes one set of rings from LPAR18SF and LPARM12SF | LP05355E | Speed 400 (Electric Only) | 2.43 |  | 0.50 in. | 0.30 in. | 1/4 in. | 0.14 oz. | 5.25 | 5.5 | Grey | 686661050716 | 0.0088 | 4.0
5.25x6.25E | Speed 400 Electric Use LPAR18SF or LPARM12SF adapter rings Includes one set of rings from LPAR18SF and LPARM12SF | LP053625E | Speed 400 (Electric Only) | 2.43 |  | 0.50 in. | 0.30 in. | 1/4 in. | 0.14 oz. | 5.25 | 6.25 | Grey | 686661050105 | 0.0088 | 4.0
5.25x6.25EC | Speed 400 Electric Carbon Use LPAR18SF or LPARM12SF adapter rings Includes one set of rings from LPAR18SF and LPARM12SF Material: 40% Carbon / 60% Nylon | LP053625EC | Speed 400 (Electric Only), Carbon Fiber (Electric Only) | 7.43 |  | 0.50 in. | 0.30 in. | 1/4 in. | 0.11 oz. | 5.25 | 6.25 | Black | 686661050198 | 0.0069 | 3.1
5.25x8E | Speed 400 Electric Use LPAR18SF or LPARM12SF adapter rings Includes one set of rings from LPARM12SF Includes Nylon spacer for hub | LP05380E | Multi Rotor (Electric Only), FPV Racing / Freestyle, Speed 400 (Electric Only) | 2.54 |  | 0.50 in. | 0.28 in. | 5 mm | 0.18 oz. | 5.25 | 8 | Grey | 686661050877 | 0.0110 | 5.0
5.25x8EP | Speed 400 Electric Pusher Reverse Rotation Use LPAR18SF or LPARM12SF adapter rings Includes one set of rings from LPARM12SF Includes Nylon spacer for hub | LP05380EP | Multi Rotor (Electric Only), FPV Racing / Freestyle, Speed 400 (Electric Only), Speed 400 Reverse Rotation (Left Hand Rotation) | 2.54 |  | 0.50 in. | 0.28 in. | 5 mm | 0.18 oz. | 5.25 | 8 | Grey | 686661050884 | 0.0110 | 5.0
5.5x2 | 049 Free Flight | LP05520 | Free Flight, Sport | 2.48 |  | 0.65 in. | 0.31 in. | 3/16 in. | 0.25 oz. | 5.5 | 2 | Grey | 686661050167 | 0.0156 | 7.1
5.5x2.5 | 049 Free Flight | LP05525 | Free Flight, Sport | 2.48 |  | 0.65 in. | 0.31 in. | 3/16 in. | 0.25 oz. | 5.5 | 2.5 | Grey | 686661050174 | 0.0156 | 7.1
5.5x4.5E | Speed 400 Electric Use LPAR18SF or LPARM12SF adapter rings Includes one set of rings from LPAR18SF and LPARM12SF | LP05545E | Multi Rotor (Electric Only), FPV Racing / Freestyle, Speed 400 (Electric Only) | 2.43 |  | 0.50 in. | 0.30 in. | 1/4 in. | 0.14 oz. | 5.5 | 4.5 | Grey | 686661050051 | 0.0088 | 4.0
5.5x4.5EP | Speed 400 Electric Pusher Reverse Rotation Use LPAR18SF or LPARM12SF adapter rings Includes one set of rings from LPAR18SF and LPARM12SF | LP05545EP | Multi Rotor (Electric Only), FPV Racing / Freestyle, Speed 400 (Electric Only), Speed 400 Reverse Rotation (Left Hand Rotation) | 2.43 |  | 0.50 in. | 0.30 in. | 1/4 in. | 0.14 oz. | 5.5 | 4.5 | Grey | 686661050112 | 0.0088 | 4.0
5.5x4.7E | Speed 400 Electric Use LPAR18SF or LPARM12SF adapter rings Includes one set of rings from LPAR18SF and LPARM12SF | LP05547E | Thin Electric, Speed 400 (Electric Only) | 2.43 |  | 0.50 in. | 0.27 in. | 1/4 in. | 0.14 oz. | 5.5 | 4.7 | Grey | 686661050709 | 0.0088 | 4.0
5.5x6.5E | Speed 400 Electric Use LPAR18SF or LPARM12SF adapter rings Includes one set of rings from LPAR18SF and LPARM12SF | LP05565E | Speed 400 (Electric Only) | 2.43 |  | 0.50 in. | 0.28 in. | 1/4 in. | 0.14 oz. | 5.5 | 6.5 | Grey | 686661050136 | 0.0088 | 4.0
5.5x6.5EC | Speed 400 Electric Carbon Use LPAR18SF or LPARM12SF adapter rings Includes one set of rings from LPAR18SF and LPARM12SF Material: 40% Carbon / 60% Nylon | LP05565EC | Speed 400 (Electric Only), Carbon Fiber (Electric Only) | 7.43 |  | 0.50 in. | 0.28 in. | 1/4 in. | 0.11 oz. | 5.5 | 6.5 | Black | 686661050204 | 0.0069 | 3.1
5.5x7.0 | 10-15 Pylon | LP05570 | Pylon Racing | 2.48 |  | 0.65 in. | 0.40 in. | 3/16 in. | 0.28 oz. | 5.5 | 7 | Grey | 686661050853 | 0.0176 | 8.0
5.7x3 | 049 Free Flight Use LPAR18SF or LPARM12SF adapter rings Includes one set of rings from LPAR18SF | LP05730 | Free Flight, Sport | 2.48 |  | 0.50 in. | 0.25 in. | 1/4 in. | 0.18 oz. | 5.7 | 3 | Grey | 686661050181 | 0.0113 | 5.1
6x2 | 049 Free Flight | LP06020 | Free Flight, Sport | 2.54 |  | 0.65 in. | 0.32 in. | 3/16 in. | 0.28 oz. | 6 | 2 | Grey | 686661060166 | 0.0175 | 7.9
6x3 | 049 Free Flight | LP06030 | Free Flight, Sport | 2.54 |  | 0.65 in. | 0.33 in. | 3/16 in. | 0.28 oz. | 6 | 3 | Grey | 686661060173 | 0.0175 | 7.9
6x3F | Folding Electric Propeller Blades Use FH35mm-6 (LPFH2-6) Hub - not included | LP06030F | Folding (Electric Only) | 3.46 |  | NA | See LPFH | See LPFH | 0.14 oz. | 6 | 3 | Grey | 686661060128 | 0.0088 | 4.0
6x3R-LH | Reversible ESC - LH, 2 Pack 3D Reversible ESC Includes two LH rotation propellers and two sets of adapter rings from LPARM12SF | LP06030R-LH | Multi Rotor (Electric Only), 3D - Reversible ESC | 3.19 |  | 0.50 in. | 0.27 in. | 5 mm | 0.14 oz. | 6 | 3 | Grey | 686661060388 | 0.0176 | 8.0
6x3R-RH | Reversible ESC - RH, 2 Pack 3D Reversible ESC Includes two RH rotation propellers and two sets of adapter rings from LPARM12SF | LP06030R-RH | Multi Rotor (Electric Only), 3D - Reversible ESC | 3.19 |  | 0.50 in. | 0.27 in. | 5 mm | 0.14 oz. | 6 | 3 | Grey | 686661060371 | 0.0176 | 8.0
6x3.1SF | Slow Flyer Indoor 3D (SF3D) For Indoor 3D Aerobatics | LP06031SF | Indoor 3D | 2.37 |  | 0.50 in. | 0.16 in. | 5 mm | 0.11 oz. | 6 | 3.1 | Grey | 686661060531 | 0.0066 | 3.0
6x4 | Sport Use LPAR18SF or LPARM12SF adapter rings Includes one set of rings from LPAR18SF | LP06040 | Sport | 2.54 |  | 0.50 in. | 0.25 in. | 1/4 in. | 0.18 oz. | 6 | 4 | Grey | 686661060180 | 0.0113 | 5.1
6x4E | Speed 400 Electric Use LPAR18SF or LPARM12SF adapter rings Includes one set of rings from LPAR18SF and LPARM12SF | LP06040E | Multi Rotor (Electric Only), FPV Racing / Freestyle, Speed 400 (Electric Only) | 2.47 |  | 0.50 in. | 0.25 in. | 1/4 in. | 0.18 oz. | 6 | 4 | Grey | 686661060104 | 0.0113 | 5.1
6x4E-B4 | Speed 400 - FPV Racing Bundle (6x4E and 6x4EP) Package contains four propellers (2 standard rotation and 2 reverse rotation) Use LPAR18SF or LPARM12SF adapter rings (optional) | LP06040E-B4 | Bundle (2 CW &amp; 2 CCW), FPV Racing / Freestyle | 5.76 |  | 0.50 in. | 0.25 in. | 5 mm | 0.18 oz. | 6 | 4 | Grey | 686661060197 | 0.0452 | 20.5
6x4EP | Speed 400 Electric Pusher Reverse Rotation Use LPAR18SF or LPARM12SF adapter rings Includes one set of rings from LPAR18SF and LPARM12SF | LP06040EP | Multi Rotor (Electric Only), FPV Racing / Freestyle, Speed 400 (Electric Only), Speed 400 Reverse Rotation (Left Hand Rotation) | 2.47 |  | 0.50 in. | 0.25 in. | 1/4 in. | 0.18 oz. | 6 | 4 | Grey | 686661060142 | 0.0113 | 5.1
6x4.1SF | Slow Flyer Indoor 3D (SF3D) For Indoor 3D Aerobatics | LP06041SF | Indoor 3D | 2.37 |  | 0.50 in. | 0.16 in. | 5.5 mm | 0.11 oz. | 6 | 4.1 | Grey | 686661060517 | 0.0066 | 3.0
6x5 | Sport Use LPAR18SF or LPARM12SF adapter rings Includes one set of rings from LPARM12SF | LP06050 | Sport | 2.54 |  | 0.65 in. | 0.33 in. | 1/4 in. | 0.25 oz. | 6 | 5 | Grey | 686661060432 | 0.0154 | 7.0
6x5.5E | Thin Electric Use LPAR18SF or LPARM12SF adapter rings Includes one set of rings from LPAR18SF and LPARM12SF | LP06055E | Thin Electric | 2.47 |  | 0.50 in. | 0.26 in. | 1/4 in. | 0.18 oz. | 6 | 5.5 | Grey | 686661060135 | 0.0113 | 5.1
6x6E | Thin Electric Use LPAR18SF or LPARM12SF adapter rings Includes one set of rings from LPAR18SF and LPARM12SF | LP06060E | Thin Electric, Multi Rotor (Electric Only), FPV Racing / Freestyle | 2.47 |  | 0.50 in. | 0.26 in. | 1/4 in. | 0.18 oz. | 6 | 6 | Grey | 686661060159 | 0.0113 | 5.1
6x6EP | Thin Electric Pusher Reverse Rotation Use LPAR18SF or LPARM12SF adapter rings Includes one set of rings from LPAR18SF and LPARM12SF | LP06060EP | Thin Electric, Multi Rotor (Electric Only), Electric Reverse Rotation (Left Hand Rotation), FPV Racing / Freestyle | 2.47 |  | 0.50 in. | 0.26 in. | 1/4 in. | 0.18 oz. | 6 | 6 | Grey | 686661060401 | 0.0113 | 5.1
6.3x4 | 15 Combat | LP06340 | Pylon Combat | 2.59 |  | 0.65 in. | 0.40 in. | 3/16 in. | 0.39 oz. | 6.3 | 4 | Grey | 686661060036 | 0.0244 | 11.1
6.5x2.9 | 10 Free Flight | LP06529 | Free Flight | 2.59 |  | 0.65 in. | 0.40 in. | 3/16 in. | 0.39 oz. | 6.5 | 2.9 | Grey | 686661060043 | 0.0244 | 11.1
6.5x3.7 | 15 Combat | LP06537 | Pylon Combat | 2.59 |  | 0.65 in. | 0.40 in. | 3/16 in. | 0.39 oz. | 6.5 | 3.7 | Grey | 686661060050 | 0.0244 | 11.1
6.5x5.0 | 10-15 Pylon | LP06550 | Pylon Racing | 2.59 |  | 0.65 in. | 0.40 in. | 3/16 in. | 0.39 oz. | 6.5 | 5 | Grey | 686661060067 | 0.0244 | 11.1
6.5x5.5 | 10-15 Pylon | LP06555 | Pylon Racing | 2.59 |  | 0.65 in. | 0.40 in. | 3/16 in. | 0.39 oz. | 6.5 | 5.5 | Grey | 686661060074 | 0.0244 | 11.1
6.5x6.0 | 10-15 Pylon | LP06560 | Pylon Racing | 2.59 |  | 0.65 in. | 0.40 in. | 3/16 in. | 0.39 oz. | 6.5 | 6 | Grey | 686661060081 | 0.0244 | 11.1
6.5x6.5 | 10-15 Pylon | LP06565 | Pylon Racing | 2.59 |  | 0.65 in. | 0.40 in. | 3/16 in. | 0.39 oz. | 6.5 | 6.5 | Grey | 686661060098 | 0.0244 | 11.1
6.5x7.0 | 10-15 Pylon | LP06570 | Pylon Racing | 2.59 |  | 0.65 in. | 0.40 in. | 3/16 in. | 0.39 oz. | 6.5 | 7 | Grey | 686661060463 | 0.0244 | 11.1
6.5x7.5 | 10-15 Pylon | LP06575 | Pylon Racing | 2.59 |  | 0.65 in. | 0.40 in. | 3/16 in. | 0.39 oz. | 6.5 | 7.5 | Grey | 686661060524 | 0.0244 | 11.1
7x10 | Sport | LP07010 | Sport | 2.65 |  | 0.65 in. | 0.41 in. | 3/16 in. | 0.46 oz. | 7 | 10 | Grey | 686661072671 | 0.0288 | 13.1
7x11E | Thin Electric Use LPAR18SF or LPARM12SF adapter rings Includes one set of rings from LPAR18SF and LPARM12SF | LP07011E | Thin Electric, Multi Rotor (Electric Only), FPV Racing / Freestyle | 2.72 |  | 0.65 in. | 0.38 in. | 5 mm | 0.35 oz. | 7 | 11 | Grey | 686661072893 | 0.0220 | 10.0
7x11EP | Thin Electric Pusher Reverse Rotation Use LPAR18SF or LPARM12SF adapter rings Includes one set of rings from LPAR18SF and LPARM12SF | LP07011EP | Thin Electric, Multi Rotor (Electric Only), Electric Reverse Rotation (Left Hand Rotation), FPV Racing / Freestyle | 2.72 |  | 0.65 in. | 0.38 in. | 5 mm | 0.35 oz. | 7 | 11 | Grey | 686661072909 | 0.0220 | 10.0
7x3 | 15 Free Flight | LP07030 | Free Flight, Sport | 2.65 |  | 0.65 in. | 0.38 in. | 3/16 in. | 0.42 oz. | 7 | 3 | Grey | 686661072596 | 0.0263 | 11.9
7x3.8WSF | Slow Flyer Wide Blade Use LPAR18SF or LPARM12SF adapter rings Includes one set of rings from LPAR18SF | LP07038WSF | Slow Fly (Electric Only) | 2.47 |  | 0.50 in. | 0.30 in. | 1/4 in. | 0.25 oz. | 7 | 3.8 | Grey | 686661070431 | 0.0156 | 7.1
7x4 | 15 Free Flight | LP07040 | Free Flight, Sport | 2.65 |  | 0.65 in. | 0.40 in. | 3/16 in. | 0.42 oz. | 7 | 4 | Grey | 686661072602 | 0.0263 | 11.9
7x4E | Thin Electric Use LPAR18SF or LPARM12SF adapter rings Includes one set of rings from LPAR18SF and LPARM12SF | LP07040E | Thin Electric, Multi Rotor (Electric Only) | 2.58 |  | 0.50 in. | 0.33 in. | 1/4 in. | 0.28 oz. | 7 | 4 | Grey | 686661070455 | 0.0176 | 8.0
7x4E(HEXO) | Hexo+ RH, 2 Pack OEM part for HEXO+ multi-copter Includes two standard rotation propellers Hub has self tightening feature for special nut Center through hole is 8mm Special Right Hand (RH) nut not included | LP07040E(HEXO) | Self Tightening, Black MR | 5.94 | Discontinued | 0.50 in. | 0.34 in. | 5 mm | 0.28 oz. | 7 | 4 | Black | 686661072695 | 0.0350 | 15.9
7x4E-B4 | Quad-Copter Bundle (7x4E and 7x4EP) Package contains four propellers (2 standard rotation and 2 reverse rotation) Use LPAR18SF or LPARM12SF adapter rings (optional) Includes four sets of rings from LPARM12SF (3mm, 5mm, 6mm,) | LP07040E-B4 | Bundle (2 CW &amp; 2 CCW) | 6.72 |  | 0.50 in. | 0.33 in. | 5 mm | 0.28 oz. | 7 | 4 | Grey | 686661072718 | 0.0704 | 31.9
7x4EP | Thin Electric Pusher Reverse Rotation Use LPAR18SF or LPARM12SF adapter rings Includes one set of rings from LPAR18SF and LPARM12SF | LP07040EP | Thin Electric, Multi Rotor (Electric Only), Electric Reverse Rotation (Left Hand Rotation) | 2.58 |  | 0.50 in. | 0.33 in. | 1/4 in. | 0.28 oz. | 7 | 4 | Grey | 686661072688 | 0.0176 | 8.0
7x4EP(HEXO) | Hexo+ LH, 2 Pack OEM part for HEXO+ multi-copter Includes two reverse rotation propellers Hub has self tightening feature for special nut Center through hole is 8mm Special Left Hand (LH) nut not included | LP07040EP(HEXO) | Self Tightening, Black MR | 5.94 | Discontinued | 0.50 in. | 0.34 in. | 5 mm | 0.28 oz. | 7 | 4 | Black | 686661072701 | 0.0350 | 15.9
7x4F | Folding Electric Propeller Blades Use FH45mm-6 (LPFH3-6) Hub - not included | LP07040F | Folding (Electric Only) | 3.66 |  | NA | See LPFH | See LPFH | 0.18 oz. | 7 | 4 | Grey | 686661070301 | 0.0113 | 5.1
7x4SF | Slow Flyer Use LPAR18SF or LPARM12SF adapter rings Includes one set of rings from LPAR18SF | LP07040SF | Multi Rotor (Electric Only), Slow Fly (Electric Only) | 2.47 |  | 0.50 in. | 0.32 in. | 1/4 in. | 0.18 oz. | 7 | 4 | Grey | 686661070363 | 0.0113 | 5.1
7x4SF-B4 | Slow Flyer Quad-Copter Bundle (7x4SF and 7x4SFP) Package contains four propellers (2 standard rotation and 2 reverse rotation) Use LPAR18SF or LPARM12SF adapter rings Includes four sets of rings from LPARM12SF (3mm, 5mm, 6mm,) | LP07040SF-B4 | Bundle (2 CW &amp; 2 CCW), Slow Fly (Electric Only) | 7.13 |  | 0.50 in. | 0.32 in. | 1/4 in. | 0.18 oz. | 7 | 4 | Grey | 686661072732 | 0.0452 | 20.5
7x4SFP | Slow Flyer Pusher Reverse Rotation Use LPAR18SF or LPARM12SF adapter rings Includes one set of rings from LPAR18SF | LP07040SFP | Multi Rotor (Electric Only), Slow Fly (Electric Only), Slow Fly Reverse Rotation (Left Hand Rotation) | 2.47 |  | 0.50 in. | 0.32 in. | 1/4 in. | 0.18 oz. | 7 | 4 | Grey | 686661072589 | 0.0113 | 5.1
7x4.1SF | Slow Flyer Indoor 3D (SF3D) For Indoor 3D Aerobatics | LP07041SF | Indoor 3D | 2.47 |  | 0.50 in. | 0.16 in. | 5.5 mm | 0.12 oz. | 7 | 4.1 | Grey | 686661072848 | 0.0077 | 3.5
7x5 | Sport | LP07050 | Sport | 2.65 |  | 0.65 in. | 0.38 in. | 3/16 in. | 0.39 oz. | 7 | 5 | Grey | 686661072619 | 0.0244 | 11.1
7x5E | Thin Electric Use LPAR18SF or LPARM12SF adapter rings Includes one set of rings from LPAR18SF and LPARM12SF | LP07050E | Thin Electric, Multi Rotor (Electric Only) | 2.58 |  | 0.50 in. | 0.33 in. | 1/4 in. | 0.28 oz. | 7 | 5 | Grey | 686661070295 | 0.0176 | 8.0
7x5E-B4 | Quad-Copter Bundle (7x5E and 7x5EP) Package contains four propellers (2 standard rotation and 2 reverse rotation) Use LPAR18SF or LPARM12SF adapter rings (optional) Includes four sets of rings from LPARM12SF (3mm, 5mm, 6mm,) | LP07050E-B4 | Bundle (2 CW &amp; 2 CCW) | 6.72 |  | 0.50 in. | 0.33 in. | 5 mm | 0.28 oz. | 7 | 5 | Grey | 686661072725 | 0.0704 | 31.9
7x5EP | Thin Electric Pusher Reverse Rotation Use LPAR18SF or LPARM12SF adapter rings Includes one set of rings from LPAR18SF and LPARM12SF | LP07050EP | Thin Electric, Multi Rotor (Electric Only), Electric Reverse Rotation (Left Hand Rotation) | 2.58 |  | 0.50 in. | 0.33 in. | 1/4 in. | 0.28 oz. | 7 | 5 | Grey | 686661070394 | 0.0176 | 8.0
7x5SF | Slow Flyer Use LPAR18SF or LPARM12SF adapter rings Includes one set of rings from LPAR18SF | LP07050SF | Slow Fly (Electric Only) | 2.47 |  | 0.50 in. | 0.35 in. | 1/4 in. | 0.18 oz. | 7 | 5 | Grey | 686661070349 | 0.0113 | 5.1
7x6 | Sport | LP07060 | Sport | 2.65 |  | 0.65 in. | 0.41 in. | 3/16 in. | 0.46 oz. | 7 | 6 | Grey | 686661072626 | 0.0288 | 13.1
7x6E | Thin Electric Use LPAR18SF or LPARM12SF adapter rings Includes one set of rings from LPAR18SF and LPARM12SF | LP07060E | Thin Electric, Multi Rotor (Electric Only) | 2.58 |  | 0.50 in. | 0.33 in. | 1/4 in. | 0.28 oz. | 7 | 6 | Grey | 686661070462 | 0.0176 | 8.0
7x6EP | Thin Electric Pusher Reverse Rotation Use LPAR18SF or LPARM12SF adapter rings Includes one set of rings from LPAR18SF and LPARM12SF | LP07060EP | Thin Electric, Multi Rotor (Electric Only), Electric Reverse Rotation (Left Hand Rotation) | 2.58 |  | 0.50 in. | 0.33 in. | 1/4 in. | 0.28 oz. | 7 | 6 | Grey | 686661072855 | 0.0176 | 8.0
7x6F | Folding Electric Propeller Blades Use FH45mm-6 (LPFH3-6) Hub - not included | LP07060F | Folding (Electric Only) | 3.66 |  | NA | See LPFH | See LPFH | 0.18 oz. | 7 | 6 | Grey | 686661072749 | 0.0113 | 5.1
7x6P | Sport Pusher | LP07060P | Sport, Pusher (for IC Engines) | 2.65 |  | 0.65 in. | 0.41 in. | 3/16 in. | 0.46 oz. | 7 | 6 | Grey | 686661072633 | 0.0288 | 13.1
7x6SF | Slow Flyer Use LPAR18SF or LPARM12SF adapter rings Includes one set of rings from LPAR18SF | LP07060SF | Slow Fly (Electric Only) | 2.47 |  | 0.50 in. | 0.32 in. | 1/4 in. | 0.18 oz. | 7 | 6 | Grey | 686661070356 | 0.0113 | 5.1
7x6W | 20 Racing Wide Blade | LP07060W | Pylon Racing | 2.70 |  | 0.65 in. | 0.41 in. | 3/16 in. | 0.46 oz. | 7 | 6 | Grey | 686661070172 | 0.0288 | 13.1
7x7 | Sport | LP07070 | Sport | 2.65 |  | 0.65 in. | 0.41 in. | 3/16 in. | 0.46 oz. | 7 | 7 | Grey | 686661072640 | 0.0288 | 13.1
7x7E | Thin Electric Use LPAR18SF or LPARM12SF adapter rings Includes one set of rings from LPAR18SF and LPARM12SF | LP07070E | Thin Electric | 2.58 |  | 0.50 in. | 0.34 in. | 1/4 in. | 0.28 oz. | 7 | 7 | Grey | 686661072800 | 0.0176 | 8.0
7x8 | Sport | LP07080 | Sport | 2.65 |  | 0.65 in. | 0.41 in. | 3/16 in. | 0.46 oz. | 7 | 8 | Grey | 686661072657 | 0.0288 | 13.1
7x9 | Sport | LP07090 | Sport | 2.65 |  | 0.65 in. | 0.41 in. | 3/16 in. | 0.46 oz. | 7 | 9 | Grey | 686661072664 | 0.0288 | 13.1
7.4x7.5C | Q40 Carbon Use LPAR06E adapter rings Includes one set of rings from LPAR06E Material: 40% Carbon / 60% Nylon | LP07475C | Carbon Fiber, AMA 422 (Q40) | 11.00 |  | 0.90 in. | 0.52 in. | 21/64 in. | 0.56 oz. | 7.4 | 7.5 | Black | 686661070400 | 0.0350 | 15.9
7.4x7.6C | Q40 Carbon Use LPAR06E adapter rings Includes one set of rings from LPAR06E Material: 40% Carbon / 60% Nylon | LP07476C | Carbon Fiber, AMA 422 (Q40) | 11.00 |  | 0.90 in. | 0.52 in. | 21/64 in. | 0.56 oz. | 7.4 | 7.6 | Black | 686661070417 | 0.0350 | 15.9
7.4x7.7C | Q40 Carbon Use LPAR06E adapter rings Includes one set of rings from LPAR06E Material: 40% Carbon / 60% Nylon | LP07477C | Carbon Fiber, AMA 422 (Q40) | 11.00 |  | 0.90 in. | 0.52 in. | 21/64 in. | 0.56 oz. | 7.4 | 7.7 | Black | 686661070424 | 0.0350 | 15.9
7.4x7.81C | Q40 Carbon Use LPAR06E adapter rings Includes one set of rings from LPAR06E Material: 40% Carbon / 60% Nylon | LP074781C | Carbon Fiber, AMA 422 (Q40) | 11.00 | Discontinued | 0.90 in. | 0.52 in. | 21/64 in. | 0.56 oz. | 7.4 | 7.81 | Black | 686661070448 | 0.0350 | 15.9
7.4x7.8C | Q40 Carbon Use LPAR06E adapter rings Includes one set of rings from LPAR06E Material: 40% Carbon / 60% Nylon | LP07478C | Carbon Fiber, AMA 422 (Q40) | 11.00 | Discontinued | 0.90 in. | 0.52 in. | 21/64 in. | 0.56 oz. | 7.4 | 7.8 | Black | 686661070370 | 0.0350 | 15.9
7.4x8.0C | Q40 Carbon Use LPAR06E adapter rings Includes one set of rings from LPAR06E Material: 40% Carbon / 60% Nylon | LP07480C | Carbon Fiber, AMA 422 (Q40) | 11.00 | Discontinued | 0.90 in. | 0.52 in. | 21/64 in. | 0.56 oz. | 7.4 | 8 | Black | 686661070226 | 0.0350 | 15.9
7.4x8.1C | Pylon Carbon Use LPAR06E adapter rings Includes one set of rings from LPAR06E Material: 40% Carbon / 60% Nylon | LP07481C | Carbon Fiber, AMA 422 (Q40) | 11.00 | Discontinued | 0.90 in. | 0.38 in. | 21/64 in. | 0.53 oz. | 7.4 | 8.1 | Black | 686661070387 | 0.0331 | 15.0
7.4x8.25C | Pylon Carbon Use LPAR06E adapter rings (not included) | LP074825C | Carbon Fiber, AMA 422 (Q40) | 11.00 | Discontinued | 0.90 in. | 0.38 in. | 21/64 in. | 0.53 oz. | 7.4 | 8.25 | Black | 686661070233 | 0.0331 | 15.0
7.5x2.5 | 15 Slow Combat | LP07525 | Combat | 2.91 | Discontinued | 0.65 in. | 0.34 in. | 3/16 in. | 0.42 oz. | 7.5 | 2.5 | Grey | 686661070158 | 0.0265 | 12.0
7.5x8C | Pylon Carbon Use LPAR06E adapter rings Includes one set of rings from LPAR06E Material: 40% Carbon / 60% Nylon | LP07580C | Pylon Racing, Carbon Fiber | 11.00 | Discontinued | 0.90 in. | 0.38 in. | 21/64 in. | 0.53 oz. | 7.5 | 8 | Black | 686661070240 | 0.0331 | 15.0
7.625x3.25 | 21-25 Free Flight | LP0763325 | Free Flight | 2.91 |  | 0.65 in. | 0.35 in. | 1/4 in. | 0.39 oz. | 7.625 | 3.25 | Grey | 686661070189 | 0.0244 | 11.1
7.8x4 | 21-25 Free Flight | LP07840 | Free Flight, Pylon Combat | 2.91 |  | 0.90 in. | 0.40 in. | 1/4 in. | 0.63 oz. | 7.8 | 4 | Grey | 686661070196 | 0.0394 | 17.9
7.8x4C | Combat Carbon Use LPAR06E adapter rings (not included) Material: 40% Carbon / 60% Nylon | LP07840C | Combat, Carbon Fiber | 19.80 | Discontinued | 0.90 in. | 0.40 in. | 1/4 in. | 0.49 oz. | 7.8 | 4 | Black | 686661070257 | 0.0306 | 13.9
7.8x6 | 36 Combat | LP07860 | Pylon Combat | 2.91 |  | 0.90 in. | 0.40 in. | 1/4 in. | 0.63 oz. | 7.8 | 6 | Grey | 686661070202 | 0.0394 | 17.9
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

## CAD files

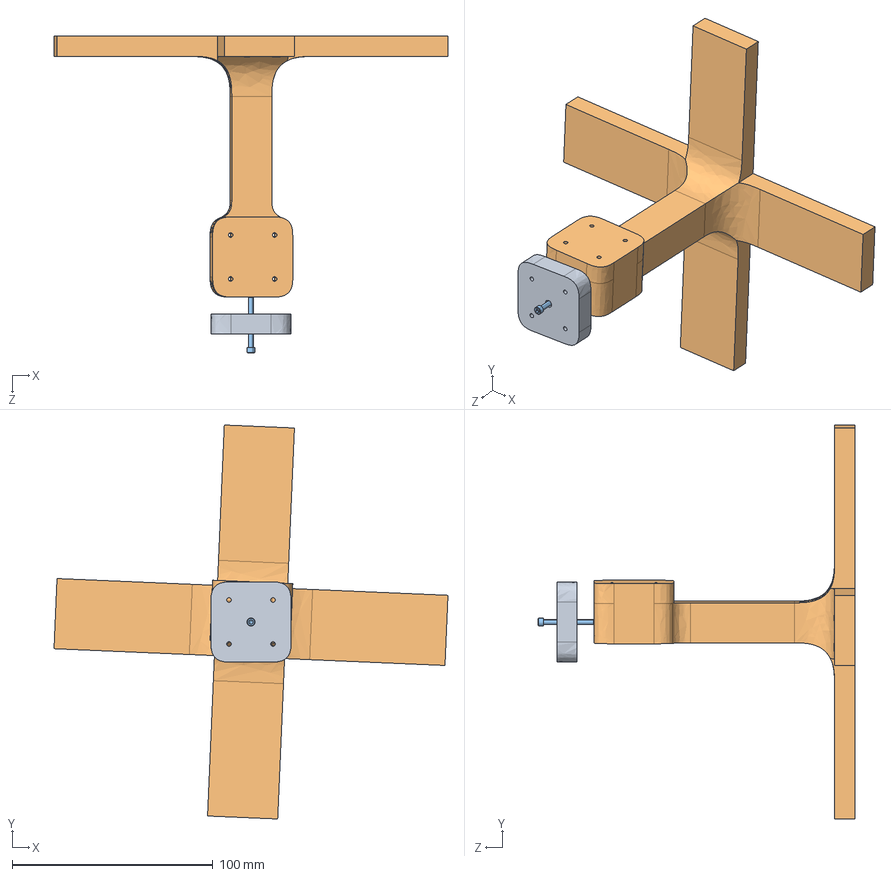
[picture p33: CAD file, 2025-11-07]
a_LivrablesEtudiants/Rendus20232024/Systeme_propulsif_et_directif/Modeles_3d/Duo/Duo_2/Assemblage2.STEP
196.3 x 196.3 x 157.7 mm
Pièce1
support_90
socket head cap screw_ai_HX-SHCS 0.099-56x1x0.75-N

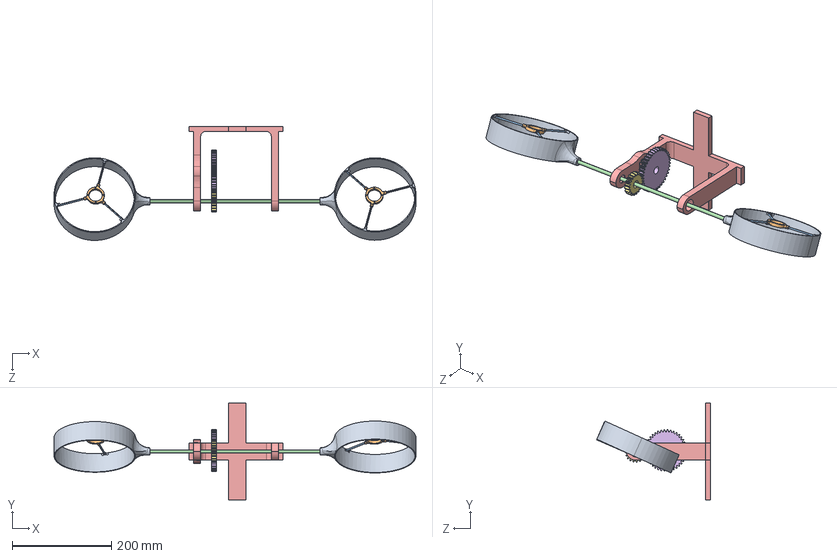
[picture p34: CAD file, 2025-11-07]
a_LivrablesEtudiants/Rendus20232024/Systeme_propulsif_et_directif/Modeles_3d/Duo/Duo_1/Assemblage2.STEP
728.0 x 195.0 x 229.2 mm
Pièce2 x 2
Fixation_moteur x 2
tige_carbon x 6
axe_7mm
support
spur gear_am_Metric - Spur gear 2M 40T 20PA 10FW ---S40N75H50L14N
spur gear_am_Metric - Spur gear 2M 20T 20PA 10FW ---S20N75H50L14N

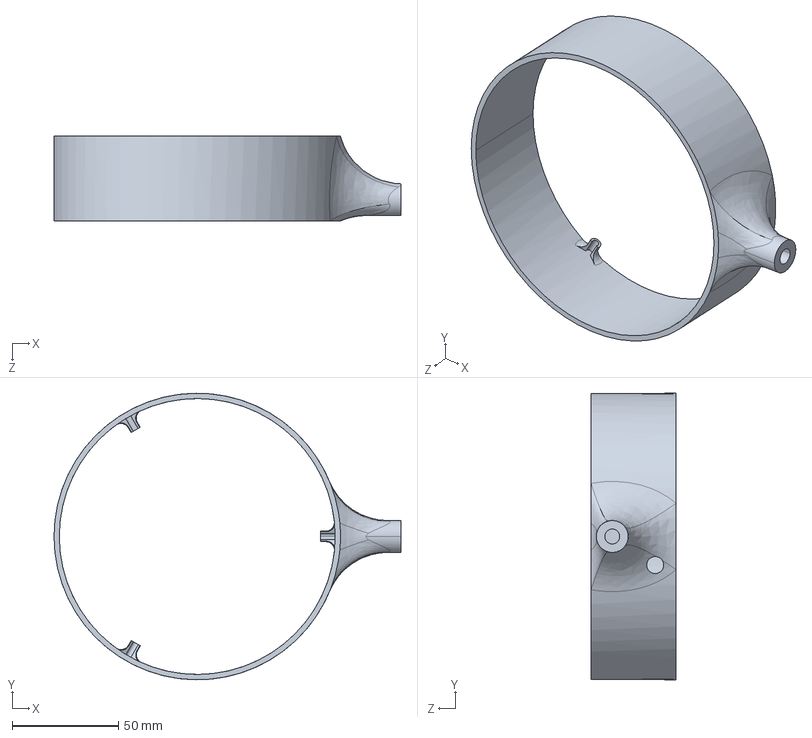
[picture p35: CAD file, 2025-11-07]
a_LivrablesEtudiants/Rendus20232024/Systeme_propulsif_et_directif/Matlab/Pièce2_Défaut_sldprt.STEP
163.5 x 135.0 x 40.0 mm

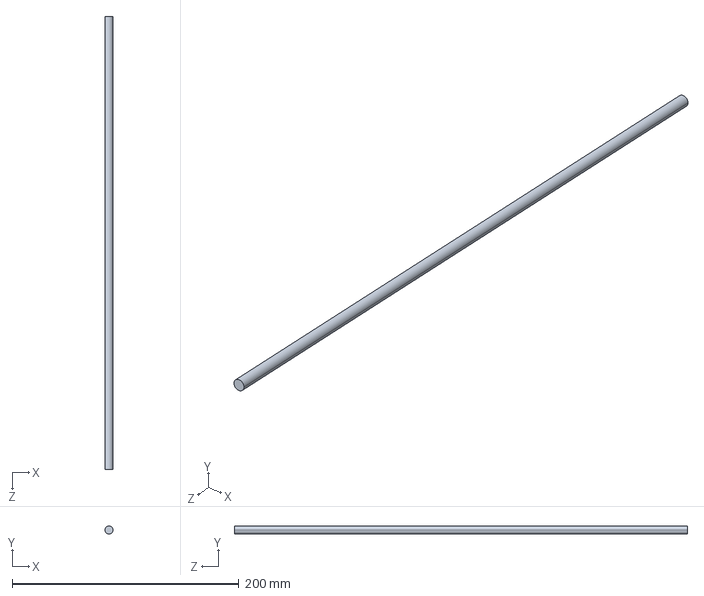
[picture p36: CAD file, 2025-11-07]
a_LivrablesEtudiants/Rendus20232024/Systeme_propulsif_et_directif/Modeles_3d/Duo/Duo_1/axe_7mm.STEP
7.00 x 7.00 x 400.0 mm

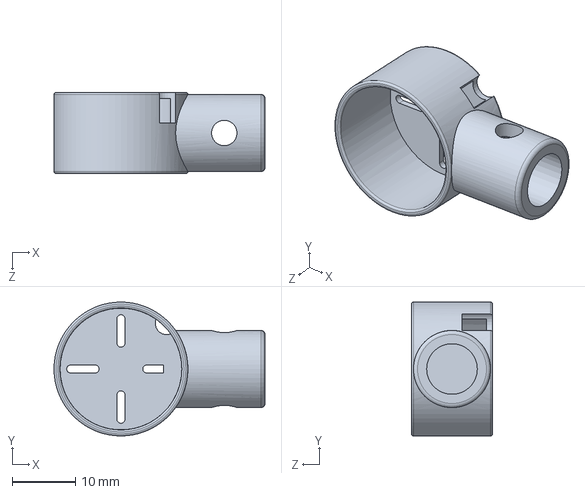
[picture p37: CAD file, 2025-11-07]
a_LivrablesEtudiants/Rendus20232024/Systeme_propulsif_et_directif/Modeles_3d/Duo/Duo_1/Solidworks/support_moteur_duo.SLDPRT
33.3 x 21.1 x 12.8 mm

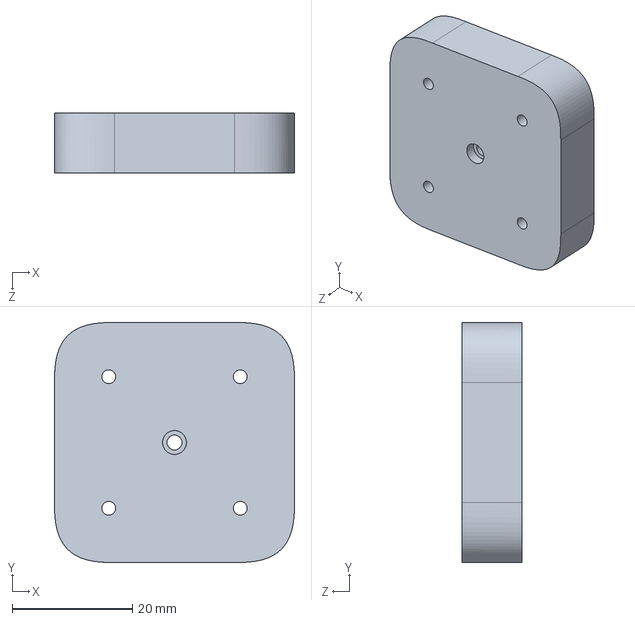
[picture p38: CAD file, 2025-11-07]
a_LivrablesEtudiants/Rendus20232024/Systeme_propulsif_et_directif/Modeles_3d/Duo/Duo_2/Pièce1.SLDPRT
40.0 x 40.0 x 10.0 mm

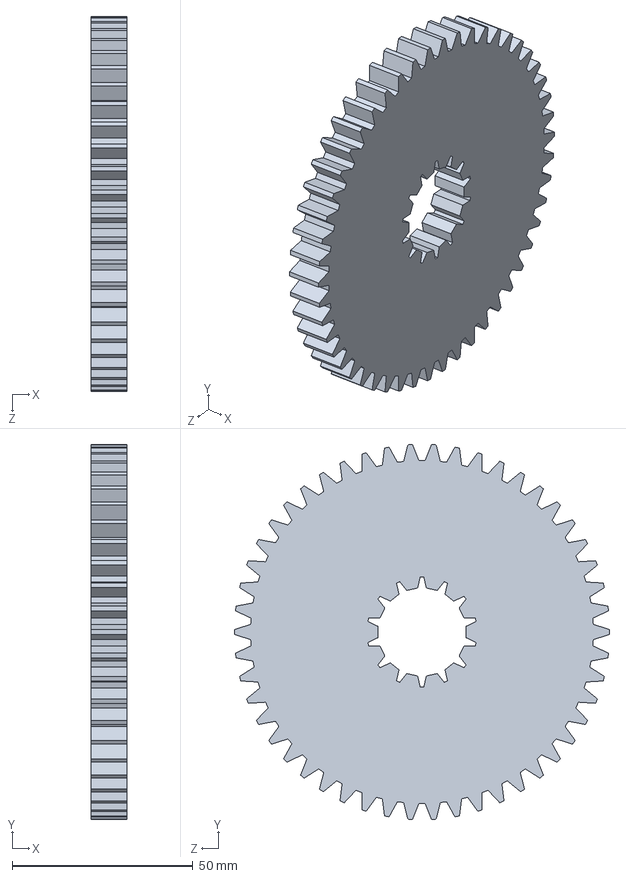
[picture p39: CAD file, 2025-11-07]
a_LivrablesEtudiants/Rendus20232024/Systeme_propulsif_et_directif/Modeles_3d/Mono/Solidworks/Gear2.SLDPRT
10.0 x 103.9 x 104.0 mm

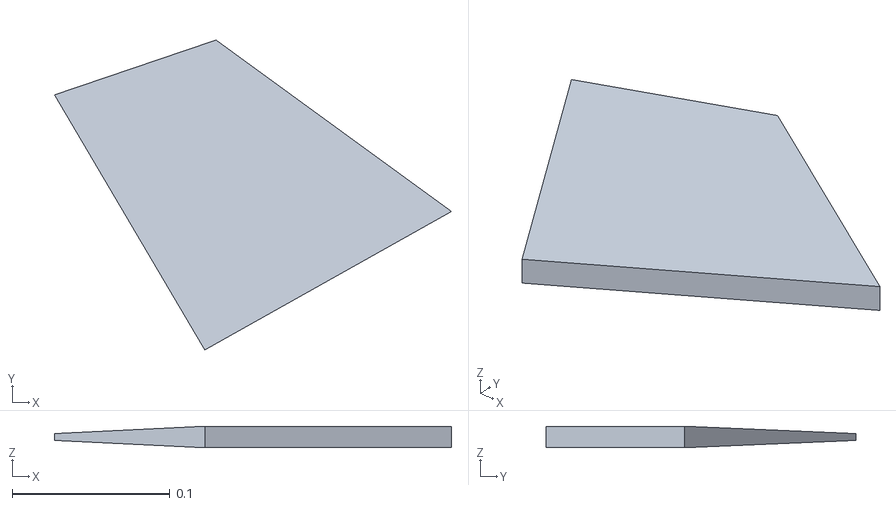
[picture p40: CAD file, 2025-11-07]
a_LivrablesEtudiants/Rendus20232024/WebBot_ressources/3D_Objects/Ailette.obj
0.252 x 0.197 x 0.0136

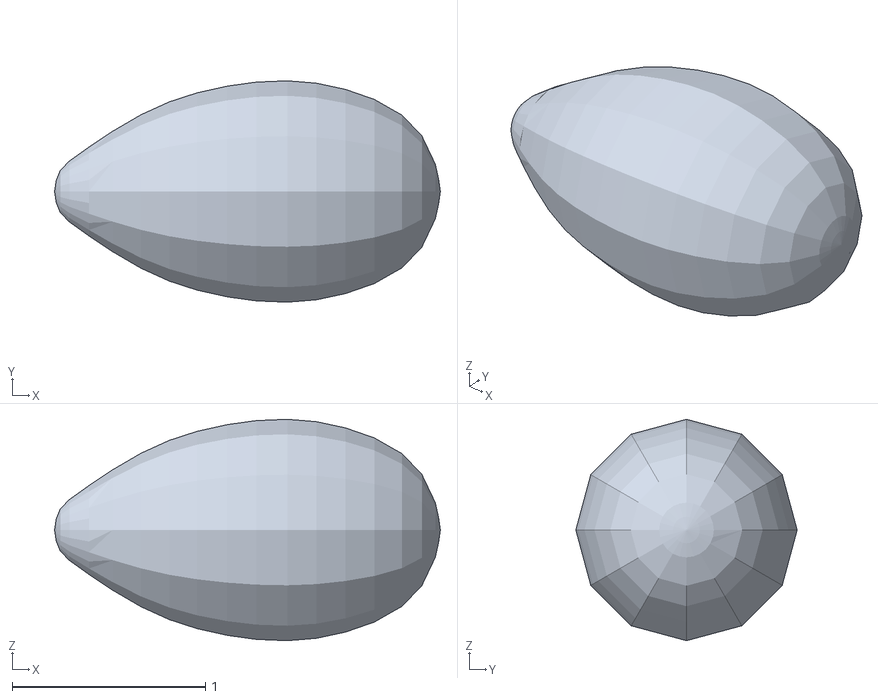
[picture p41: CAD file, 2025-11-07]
a_LivrablesEtudiants/Rendus20232024/WebBot_ressources/worlds/Enveloppe.obj
2.00 x 1.14 x 1.14

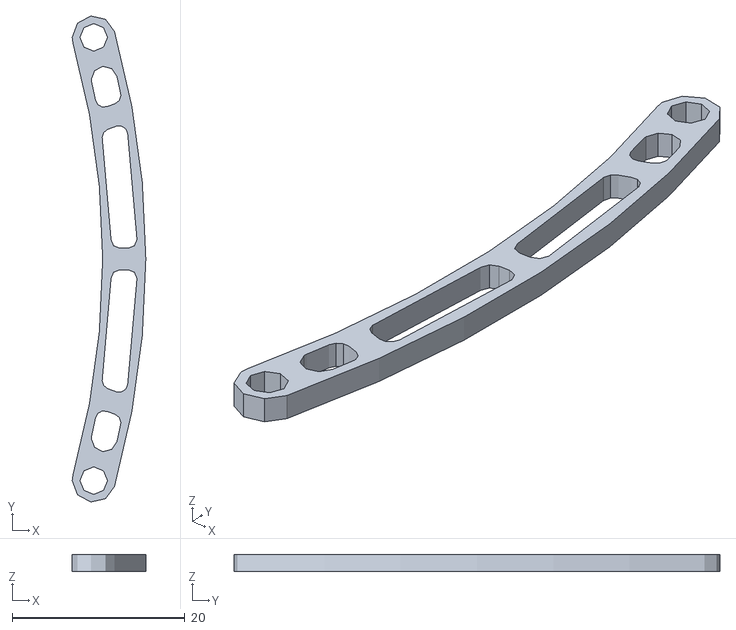
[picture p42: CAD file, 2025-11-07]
a_LivrablesEtudiants/Rendus20242025/CoBraPID_Catia/impression/Pince/04-Raccord2.stl
8.54 x 56.3 x 2.00

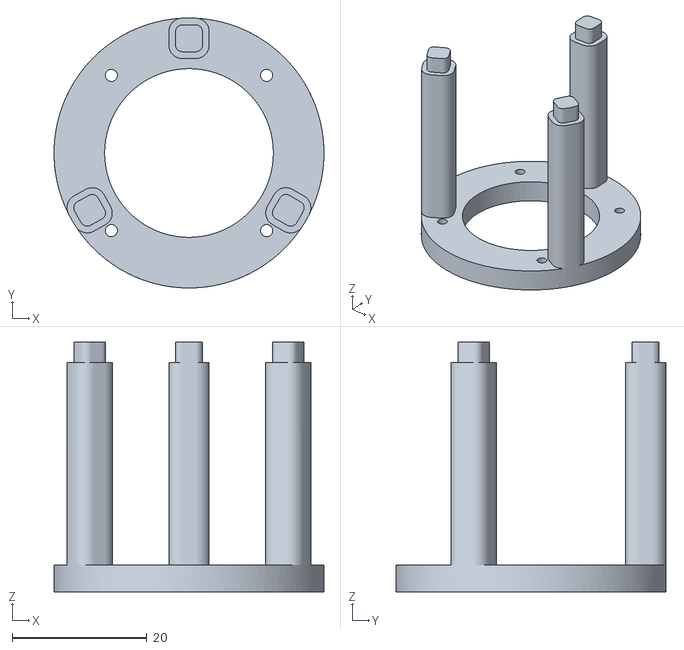
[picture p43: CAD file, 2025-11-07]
a_LivrablesEtudiants/Rendus20242025/CoBraPID_Catia/impression/support mot bas fixation.stl
40.0 x 40.0 x 37.0

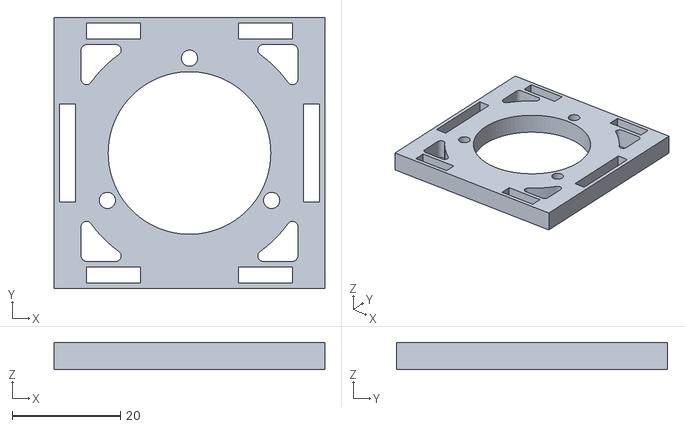
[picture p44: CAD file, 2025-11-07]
a_LivrablesEtudiants/Rendus20242025/CoBraPID_Catia/impression/Treuil/Treuil plateforme.stl
50.0 x 50.0 x 5.00

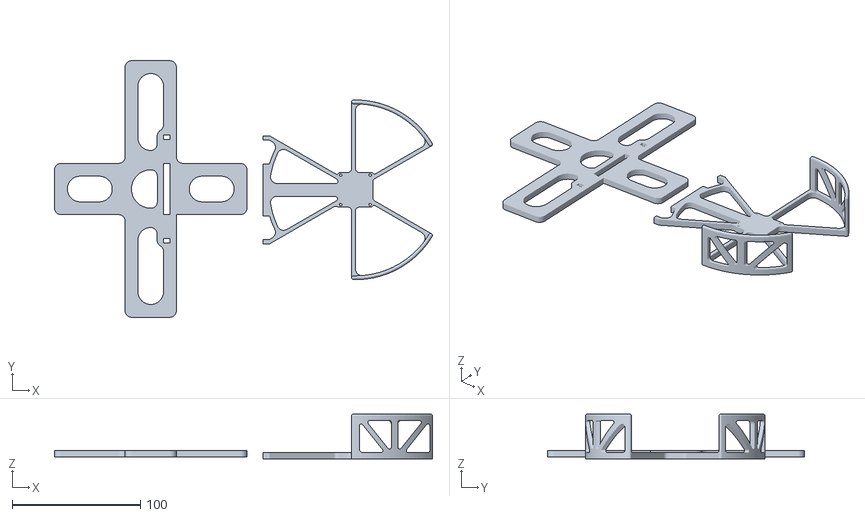
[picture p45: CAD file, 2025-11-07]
a_LivrablesEtudiants/Rendus20242025/CoBraPID_Catia/Support moteurs lat imprimables.stl
294.6 x 200.0 x 35.0

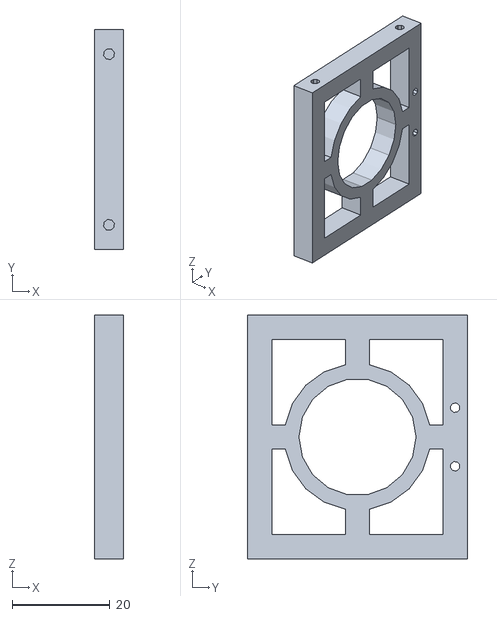
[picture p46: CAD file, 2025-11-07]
a_LivrablesEtudiants/Rendus20242025/meca_propulsion_treuil/CAO/treuil/pièces stl/treuil montant 1.stl
6.00 x 45.0 x 50.0

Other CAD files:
a_LivrablesEtudiants/Rendus20232024/Systeme_propulsif_et_directif/Modeles_3d/Duo/Duo_1/Solidworks/Assemblage_duo.SLDASM
a_LivrablesEtudiants/Rendus20232024/Systeme_propulsif_et_directif/Modeles_3d/Mono/Solidworks/Assemblage_mono.SLDASM
a_LivrablesEtudiants/Rendus20242025/meca_propulsion_treuil/Dirigeable.SLDPRT
a_LivrablesEtudiants/Rendus20232024/Etude 1 centre gravite et matrice d'inertie/Modele CATIA/Fichiers CATIA/dirigeable assemblage helium+enveloppe.CATProduct
a_LivrablesEtudiants/Rendus20232024/Etude 1 centre gravite et matrice d'inertie/Modele CATIA/Fichiers CATIA/dirigeable catia.CATPart
a_LivrablesEtudiants/Rendus20232024/Etude 1 centre gravite et matrice d'inertie/Modele CATIA/Fichiers CATIA/enveloppe interne.CATPart
a_LivrablesEtudiants/Rendus20232024/Systeme_propulsif_et_directif/Matlab/axe_7mm_Défaut_sldprt.STEP
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

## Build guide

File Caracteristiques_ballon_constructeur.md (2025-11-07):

| Caractéristiques | Valeur | Commentaire |
|:---| ---:|---|
| Masse enveloppe | 1.3 kg | Mesurée le 23/01/2024 par Mathias L. |
| Longueurs demi-grand axe | 142x275cm | Mesurée le 16/02/2024 par Mathias L. |

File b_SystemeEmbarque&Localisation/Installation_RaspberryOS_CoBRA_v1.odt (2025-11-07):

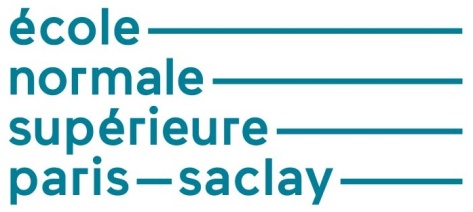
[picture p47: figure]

Installation de Raspberry OS sur Raspberry Pi Zéro 2 W Anthony JUTON¹
| Version 1 du 10/10/2024

Le nano-ordinateur Raspberry Pi Zéro 2 W est utilisé sur le dirigeable comme un serveur « Headless », c’est à dire sans écran ni clavier. On y accède par un bureau virtuel ou par une console depuis un PC personnel. Ce document présente l’installation de Raspberry OS et les outils nécessaires pour un accès au nano-ordinateur, sans écran ni clavier.

Attention, des Raspberry Pi Zéro sont aussi utilisées pour des tests. Vérifier les références de sa carte avant installation.

Les informations concernant la carte Raspberry Pi 4 sont disponibles sur le site de Raspberry : https://www.raspberrypi.com/products/raspberry-pi-zero-2-w/

# Installation de l’OS

## Création de l’image

Le site Raspberry explique en détail comment installer le système d’exploitation sur la PI Zero.

Pour installer Raspberry OS sur la carte, on crée une image du système d’exploitation sur la carte SD du nano-ordinateur via un PC personnel.

Pour créer cette image, on insère la carte SD dans le PC et on commence par télécharger Raspberry Pi Imager : https://www.raspberrypi.com/software/

On choisit Raspberry OS 64bits et la carte SD.

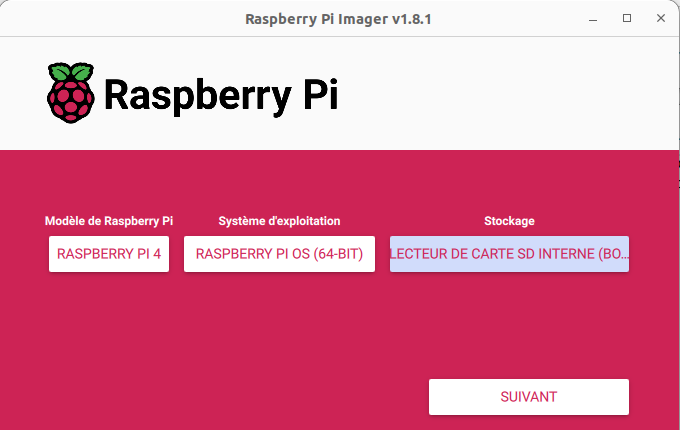
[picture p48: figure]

Figure 1: Fenêtre du logiciel Raspberry Imager avant écriture de la carte SD

Le bouton Suivant puis l’option Modifier les réglages permettent d’ajouter une configuration de connexion au réseau WIFI (ce peut être un point d’accès WIFI créé par un smartphone) en indiquant un nom de réseau Wifi (SSID) et la clé WPA associée (password). Activer également SSH (pour un accès à distance)

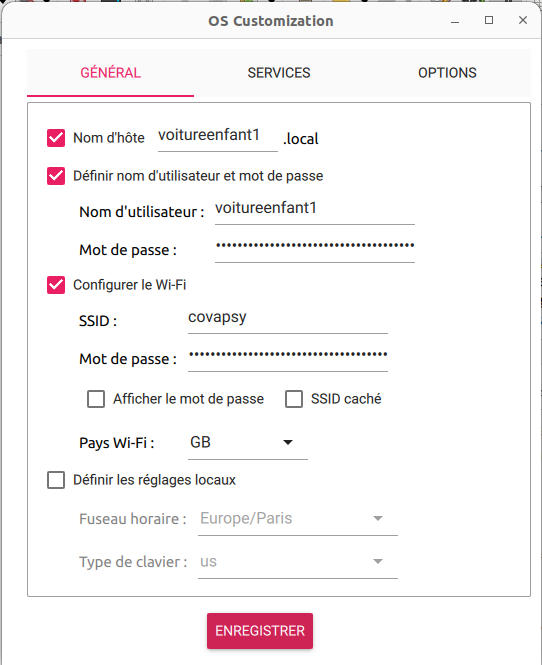
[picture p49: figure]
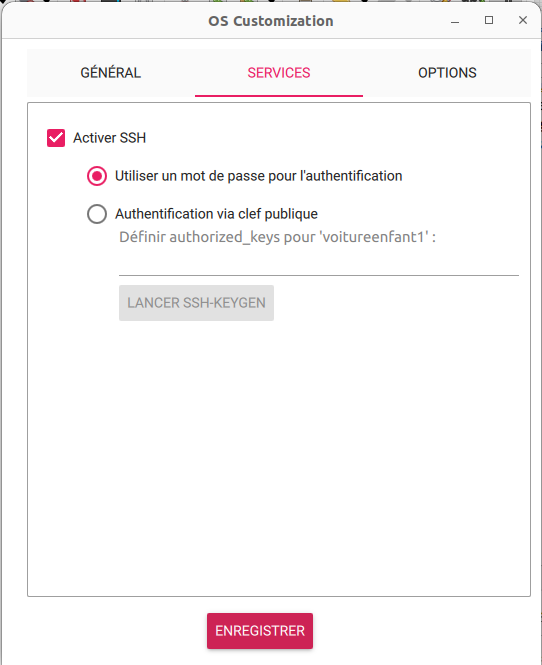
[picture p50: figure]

Figure 2 : Paramètres de l'image Raspberry OS

Attention, le nano-ordinateur se trouvant connecté à Internet, il est nécessaire de ne surtout pas laisser le login pi associé au mot de passe raspberry.

La configuration est terminée. Cliquer sur Enregistrer puis Yes à la demande d’appliquer les modifications. Générer la carte (bouton Ecrire) et l’insérer dans la raspberry pi.

## Recherche de l’IP du nano-ordinateur

Une fois ces configurations effectuées et l’alimentation (port micro-usb PWR), le nano-ordinateur démarre, connecté via le WIFI configuré lors de la préparation de la carte SD à un routeur apte à lui donner une adresse IP (la box de la maison ou un routeur du commerce). Pour s’y connecter à distance, il est alors nécessaire d’avoir son adresse IP, adresse notée sous la forme de 4 nombres 192.168.1.4 par exemple (en IPv4).

Le PC doit être bien évidemment connecté sur le même réseau local (en Wifi ou en Ethernet).

- Il est possible de connecter un écran sur le port mini-hdmi et un clavier et une souris. Cette solution demandant du matériel supplémentaire et peu ergonomique pour la suite, ce document se concentre sur les solutions headless.
- Une solution simple est de faire un ping avec une recherche DNS locale, depuis une console (nommée invite de commande sous windows) avec le hostname défini dans la partie précédente : ping voitureenfant1.local

Le nano-ordinateur répond alors avec son adresse IP.

Figure 3 : Réponse à une recherche DNS locale

- On peut aussi trouver l’adresse IP du nano-ordinateur sur la page d’accueil du routeur (à condition d’y avoir un accès). Pour cela, on se rend sur la page web de la box ou du routeur (la page web de la box internet, pour une utilisation à domicile, est souvent accessible à l’adresse 192.168.1.1).

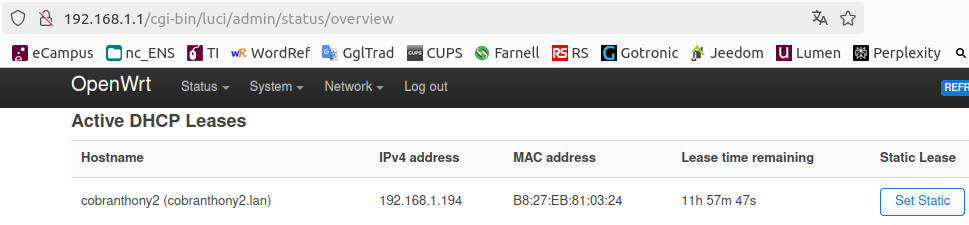
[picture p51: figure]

  Figure 4: Page d'accueil du routeur OpenWRT avec une carte raspebrry pi de connectée. Le bouton "Set static" permet de réserver l'adresse.

On présente ci-dessous les pages d’une LiveBox. Les routeurs grand public et les box ont la même apparence avec une vue globale (overview) du réseau local où on trouve les IP des équipements connectés et des pages de configuration avancée (parfois nommées LAN network), notamment pour la réservation des adresses IP.

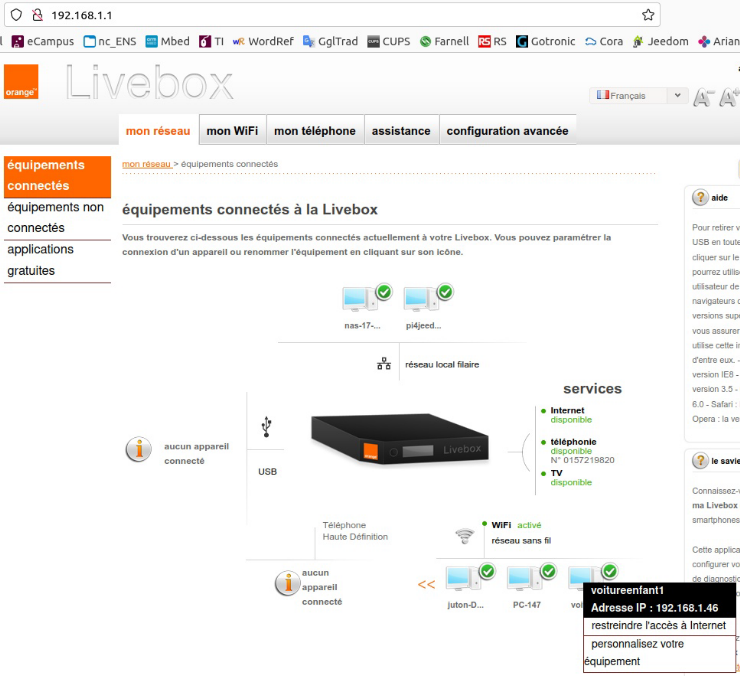
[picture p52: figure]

Figure 5 : Présentation des équipements connectés au réseau par une LiveBox

Il est alors possible de réserver l’adresse IP dans le serveur DHCP, de sorte que le nano-ordinateur obtienne toujours la même adresse lors de ces nouvelles connexions.

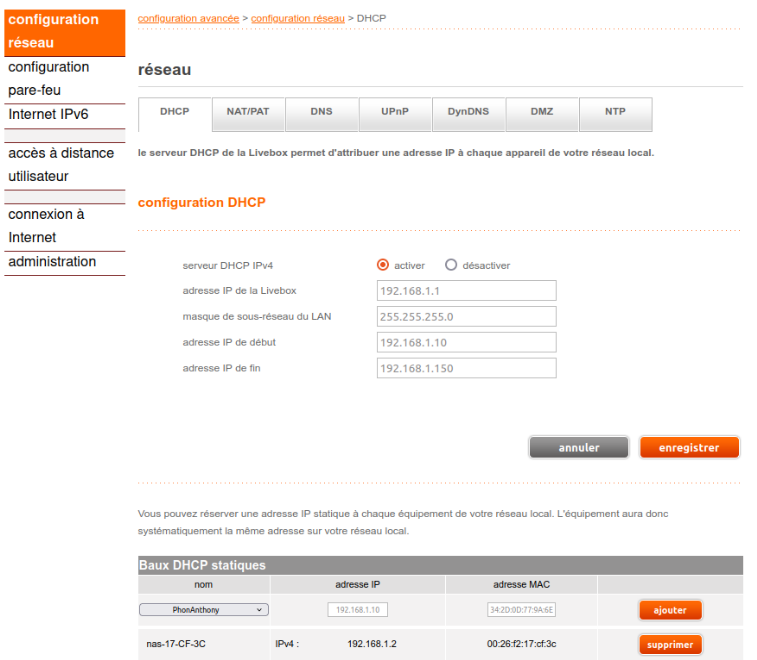
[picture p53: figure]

Figure 6 : Page de configuration DHCP d’une livebox où sont attribuées les adresses IP statiques (ou IP réservées)

## Connexion SSH

Une fois l’IP découverte, il est aisé de se connecter en SSH (Secure Shell). SSH est un protocole de communication sécurisé permettant de dialoguer via une console du serveur SSH ouverte sur le client SSH. Le nano-ordinateur est serveur SSH et le PC utilisateur est client SSH.

Très utile pour les accès à distance, le serveur SSH est installé par défaut sur les Raspberry Pi (et il a été activé dans les options lors de la création de la carte SD).

Le client SSH est installé sur les PC Linux (et sans doute Mac). Sur les PC Windows, l’invite de commande permet désormais de faire du ssh. On peut installer Putty sinon.

Depuis une console (terminal Linux ou invite de commande sous Windows), on tape :

ssh login@<adresse IP de la raspberry pi>

L’authenticité de ce serveur SSH n’étant pas attesté, une demande de confirmation attend la réponse yes, lors de la première connexion, puis le mot de passe de l’utilisateur.

Lorsque la connexion est réussie, le prompt indique :

le_nom_de_l_utilisateur@le_nom_de_la_machine, ici voitureenfant1@voitureenfant1

La commande exit permet de couper la connexion.

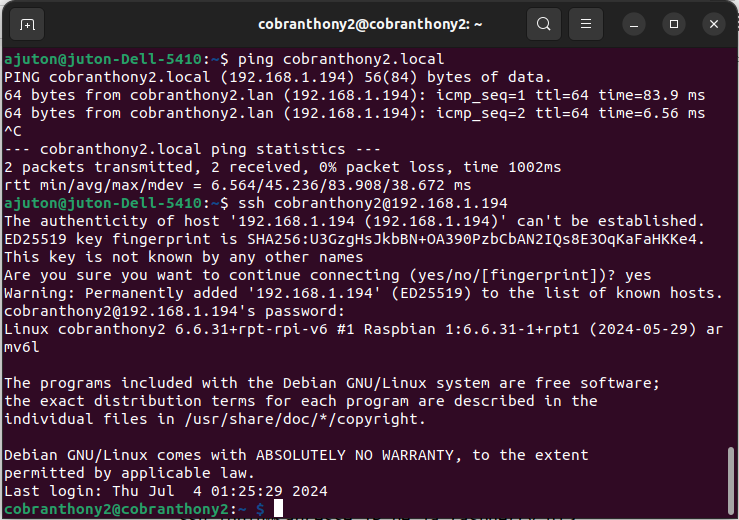
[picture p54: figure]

Figure 7: Connexion ssh à la Raspberry pi depuis un PC relié sur le même réseau local

### Copie de fichiers à distance scp

Il est possible d’utiliser ssh pour transférer des fichiers entre l’ordinateur (PC) et le nano-ordinateur (raspberry pi). La commande s’appelle scp pour ssh copy.

Pour copier un fichier depuis le PC vers le dossier Documents de la raspberry pi. On se place dans le dossier correspondant du PC (sous linux, on clique droit dans le dossier dans l’explorateur de Fichier et on choisit Ouvrir dans un terminal). Sous windows, il est possible de se déplacer dans les dossiers depuis l’invite de commande avec la commande cd (change directory) :

scp nom_du_fichier le_nom_de_l_utilisateur@le_nom_de_la_machine:Documents

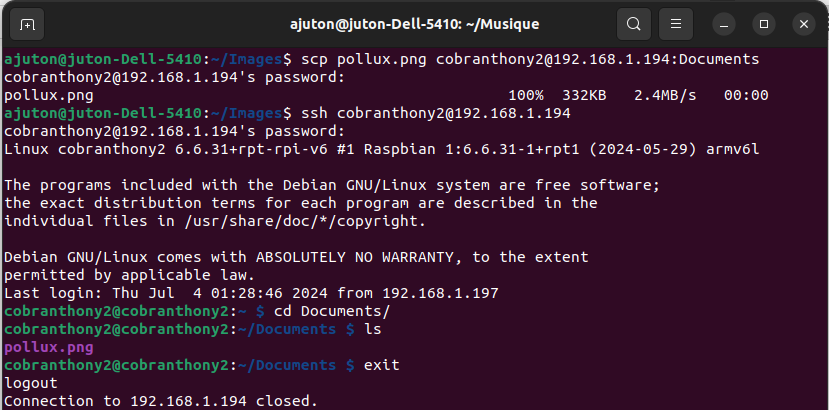
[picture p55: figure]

Figure 8: Console d'une copie de fichier du PC vers la raspberry Pi

Pour copier un fichier depuis le dossier Documents de la raspberry pi vers le PC :

scp le_nom_de_l_utilisateur@le_nom_de_la_machine:Documents/nom_du_fichier .

Le point à la fin permet d’indiquer que le fichier doit être déposé à l’emplacement d’où l’on envoie la commande scp.

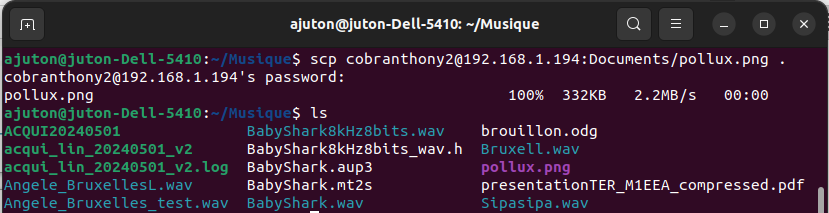
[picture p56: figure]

Figure 9: Copie depuis le PC d'un fichier de la raspberry Pi vers un dossier du PC

# Bureau à distance

Pour faciliter l’utilisation du nano-ordinateur dans un premier temps, les outils graphiques sont plus accessibles que la ligne de commande. Celui-ci étant gourmand en ressource, il peut être intéressant de le désactiver une fois que la configuration est correcte et qu’il n’y a que du code à écrire.

### 2.1 Mise en œuvre d’un bureau à distance VNC

VNC (Virtual Network Computing) est un protocole de bureau à distance. Le serveur VNC est la Raspberry Pi et le client VNC est le PC utilisateur.

Le site raspberrypi.com propose là encore des solutions :

https://www.raspberrypi.com/documentation/computers/remote-access.html#virtual-networkcomputing-vnc

### 2.1.1 Installation du client sur le PC

Raspberry propose la solution gratuite mais propriétaire de RealVNC. Il est possible de télécharger le client vnc (nommé VNC Viewer) : sur le site (https://www.realvnc.com/en/), onglet Download, choisir la version adaptée de VNC Viewer à l’OS de l’ordinateur et l’installer.

### 2.1.2 Activation du serveur VNC sur le nano-ordinateur Raspberry Pi

Realvnc-vnc-serveur est installé avec l’image de Raspberry OS. Pour l’activer, utiliser la fenêtre de configuration raspi-config, depuis l’accès SSH :

sudo raspi-config

Ensuite, choisir Interface Options > VNC › Yes.

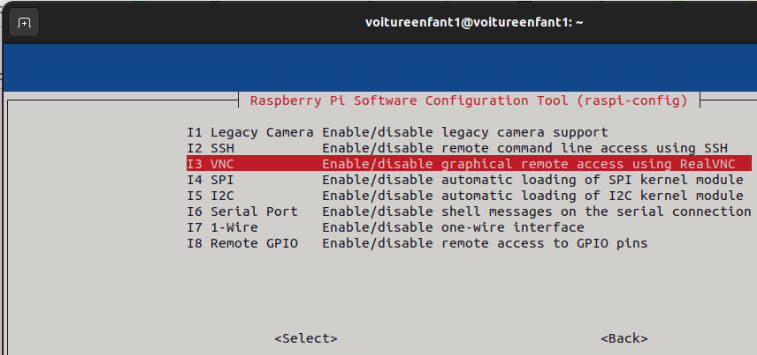
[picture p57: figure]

Figure 10 : Extrait de la fenêtre raspi-config

Enfin, aller sur Ok puis Finish pour fermer raspi-config.

### 2.1.3 Connexion locale au serveur vnc

Pour se connecter en VNC depuis un PC connecté sur le même réseau que le nano-ordinateur, lancer VNC Viewer, indiquer l’adresse IP de la Raspberry Pi, accepter les recommandations de précautions, introduire son login et son mot de passe.

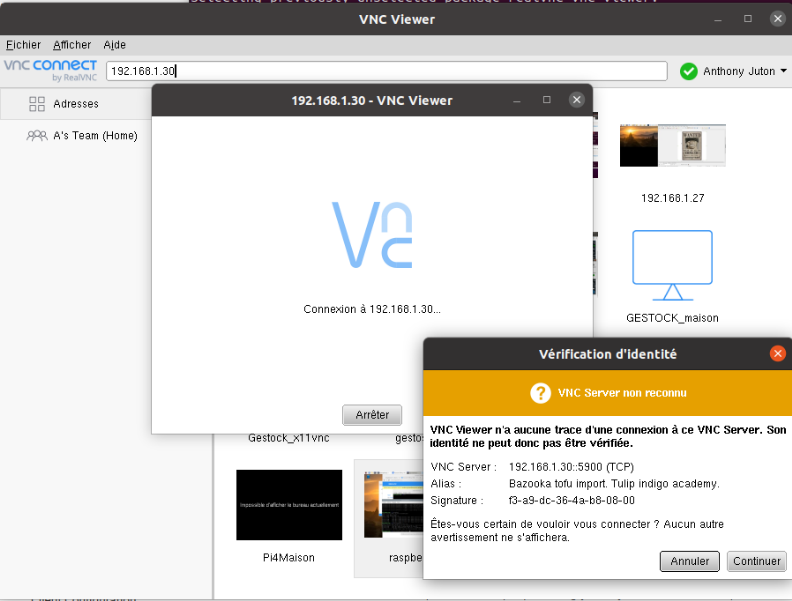
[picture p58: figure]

Figure 11 : Client VNC Viewer lors de la 1ère connexion à la Raspberry Pi

On accède alors au bureau à distance, qui lors de la première connexion demande à faire quelques mises à jour. Suite à un redémarrage on peut profiter du bureau à distance du nano-ordinateur.

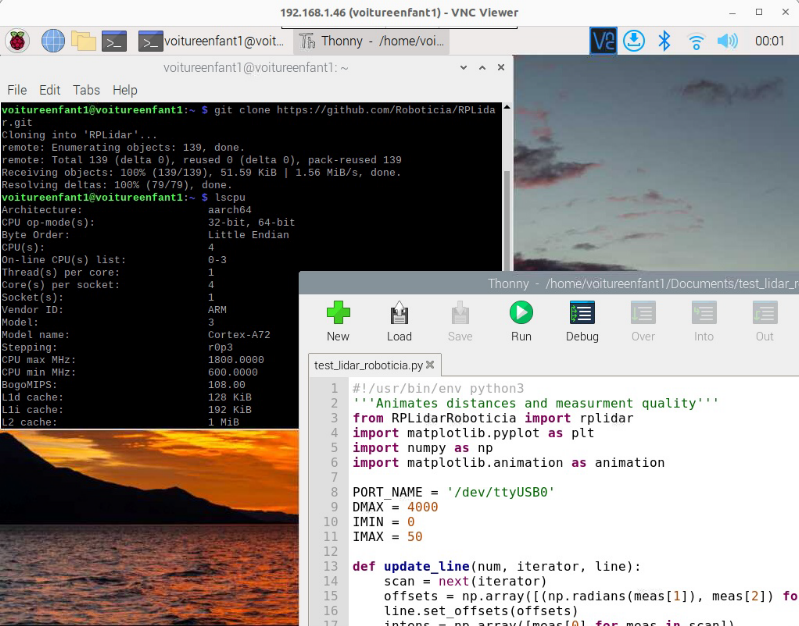
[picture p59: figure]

Figure 12 : Bureau à distance de la Raspberry Pi via RealVNC

Depuis le bureau à distance, il est possible d’ajouter ou retirer des réseaux wifi (par exemple celui du PC ou du smartphone de l’étudiant) : clic sur l’icône wifi puis Advanced Options puis Edit Connections...

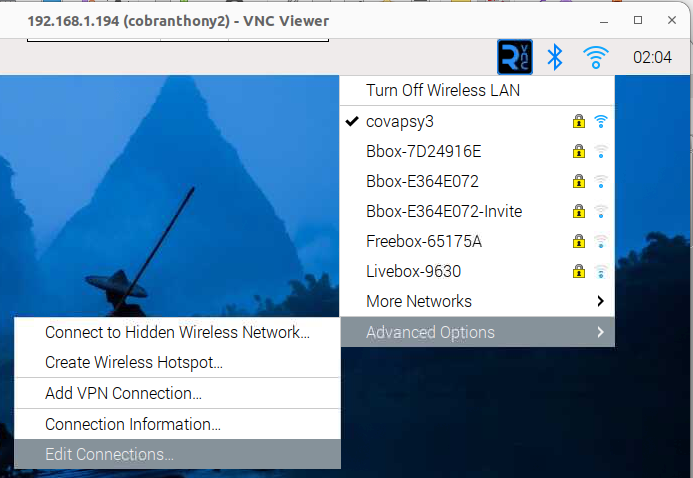
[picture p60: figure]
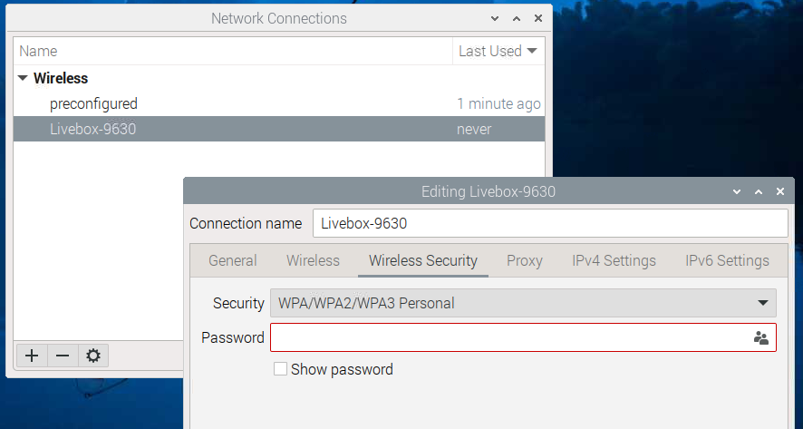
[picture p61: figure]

Figure 13: Configuration d'un 2nd réseau wifi depuis le bureau à distance

# Utiliser les entrées/sorties

Pour utiliser les périphériques de communications, il faut les activer via la fenêtre Raspberry Pi Configuration (Menu Raspberry > Preferences > Raspberry Pi Configuration). Sont utilisées ici ssh, VNC et i2c. Les mêmes configurations peuvent se faire depuis raspi-config, depuis une console ssh.

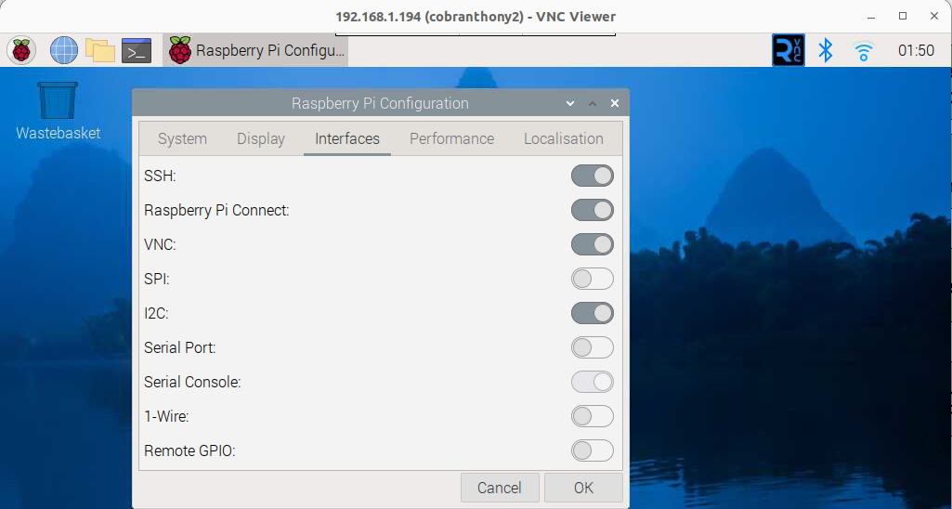
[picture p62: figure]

Figure 14: Activation des bus i2c et SPI via Raspberry Pi Configuration

Depuis l’interface graphique, il est possible d’ajouter une manette bluetooth (ou un autre périphérique bluetooth).

- Commencer par mettre la manette en mode Discoverable : appuyer sur Share et P en même temps jusqu’à avoir un clignotement rapide.
- Sur la Raspberry Pi, cliquer sur l’icône Bluetooth puis Add Device.
- Lorsque la manette (Wireless Controller) est découverte, la sélectionner et cliquer sur Pair.
- Si tout se passe bien, la manette passe en lumière bleu foncé fixe et la raspberry Pi annonce Pairing succesfull.

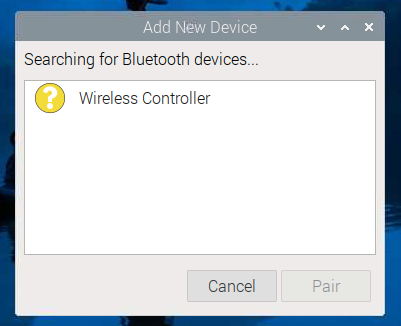
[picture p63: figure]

Figure 15: Association bluetooth d'une manette à la raspberry pi

## Installation des paquets utiles

Pour le bon fonctionnement du dirigeable, quelques paquets Linux sont utiles. Ils seront présentés plus loin. Pour plus d’efficacité, il est préférable de fermer VNC Viewer et de faire ces actions depuis une console SSH.

Depuis la console, lancer les commandes d’installation suivantes pour mettre à jour le système et installer la bibliothèque matplotlib :

sudo apt update && sudo apt upgrade -y

sudo apt install python3-matplotlib -y

pip install pyPS4Controller --break-system-packages

Remarque : Python demande désormais par défaut d’utiliser des environnements virtuels. La raspberry Pi ne servant qu’à la conduite autonome, on peut installer les modules python hors environnement virtuel, soit en installant le paquet depuis les dépôts linux officiels de la distribution :

sudo apt install python3-nomdumodule

ou

pip install nomdumodule --break-system-packages

# Programmation python

Le nano-ordinateur raspberry Pi étant un ordinateur sous linux, plusieurs solutions sont possibles pour programmer et exécuter du code python.

Depuis le bureau à distance.

L’éditeur python Thonny est léger et est installé par défaut sur raspberry OS. Il suffit de le lancer depuis l’interface graphique pour exécuter du code. Il possède un débogueur qui permet d’exécuter le code pas à pas.

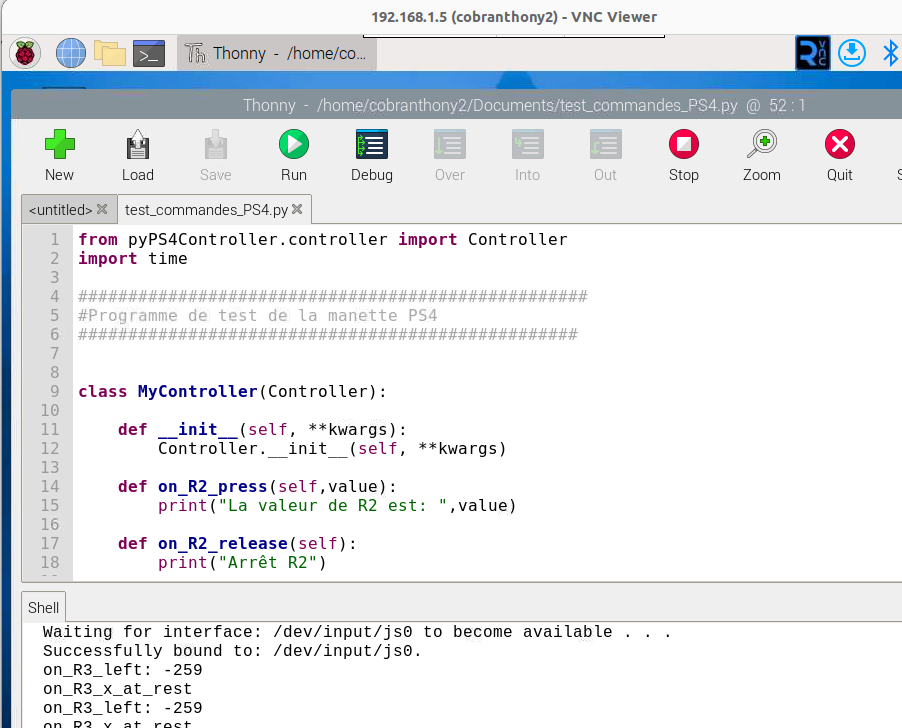
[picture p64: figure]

Figure 16: Exécution d'un code python depuis Thonny, sur le bureau à distance

Depuis une console ssh.

VNC étant gourmand en ressource, on essaie de s’en passer lorsqu’il apporte peu. Depuis une console ssh, il est possible d’éditer du code avec nano et de l’exécuter avec la commande python3.

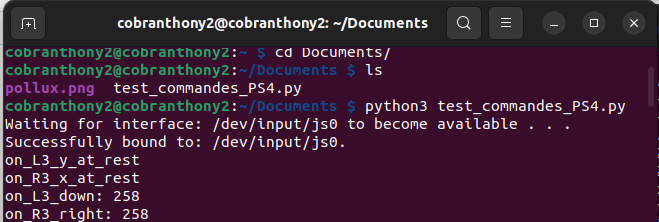
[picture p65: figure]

Figure 17: Exécution d'un programme python depuis une console ssh

Depuis VS Code sur un PC.

VSCode (tout comme pyCharm) permet d’exécuter et déboguer du code sur une machine distante (raspberry pi Zéro 2 au minimum) accessible en ssh.

Installer VSCode et ses extensions python et remote-SSH.

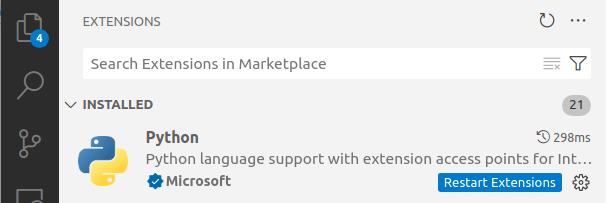
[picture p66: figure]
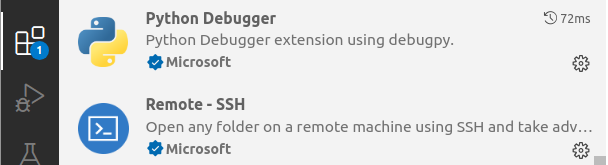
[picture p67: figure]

Sa connecter à la carte via l’icône Remote Explorer puis ajouter à ssh le connexions souhaitées.

# Premiers programmes

Le programme test_commande_PS4.py récupère et affiche les commandes de la manette PS4.

Le programme test_bno055.py affiche quelques données de la centrale inertielle

Pour contrôler les servo-moteur, on utilise un composant PCA9685. Son code est disponible sur la page : https://github.com/adafruit/Adafruit_Python_PCA9685

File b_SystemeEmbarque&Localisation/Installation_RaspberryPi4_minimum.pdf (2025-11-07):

Informatique embarquée

# Installation de Raspberry OS

# sur Raspberry Pi 4

Anthony Juton, juin 2023

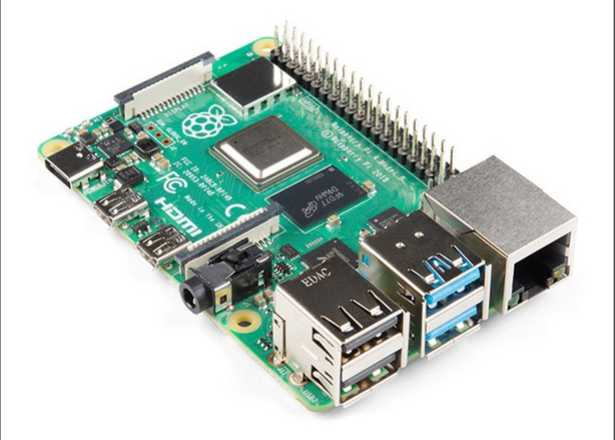
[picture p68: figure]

Le nano-ordinateur Raspberry Pi 4 peut être utilisé comme un PC avec écran et clavier. Il est

utilisé ici comme un serveur « Headless », c’est à dire sans écran ni clavier. On y accède par un

bureau virtuel ou par une console depuis un PC personnel.

Ce document présente l’installation de Raspberry OS et les outils nécessaires pour un accès au

nano-ordinateur, sans écran ni clavier.

Les informations concernant la carte Raspberry Pi 4 sont disponibles sur le site de Raspberry :

https://www.raspberrypi.com/products/raspberry-pi-4-model-b/

## 1 Installation l’OS

### 1.1 Création de l’image

Le site Raspberry explique en détail comment installer le système d’exploitation sur la PI 4.

Pour installer Raspberry OS sur la carte, on crée une image du système d’exploitation sur la

carte SD du nano-ordinateur via un PC personnel.

Pour créer cette image, on insère la carte SD dans le PC et on commence par télécharger

Raspberry Pi Imager : https://www.raspberrypi.com/software/

On choisit Raspberry OS 64bits et la carte SD.

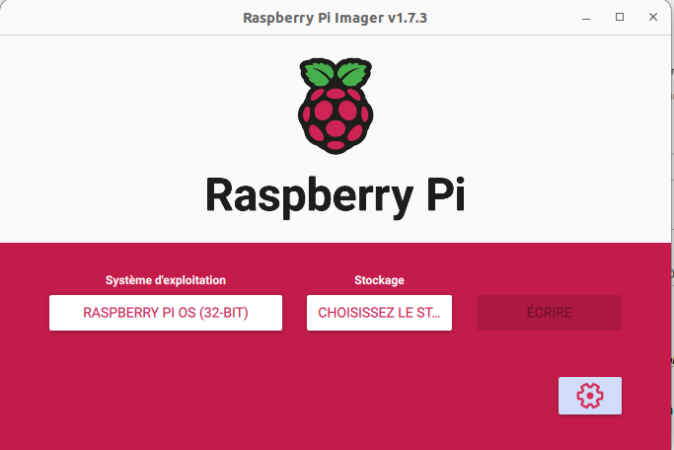
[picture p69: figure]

Figure 1: Fenêtre du logiciel Raspberry Imager avant

écriture de la carte SD

Installation de Raspberry OS sur Raspberry Pi 4 | 1

L’icône engrenage permet d’ajouter une configuration de connexion au réseau WIFI (ce peut

être un point d’accès WIFI créé par un smartphone). Activer également SSH (pour un accès à

distance) et indiquer un nom de réseau Wifi (SSID) et la clé WPA associée (password).

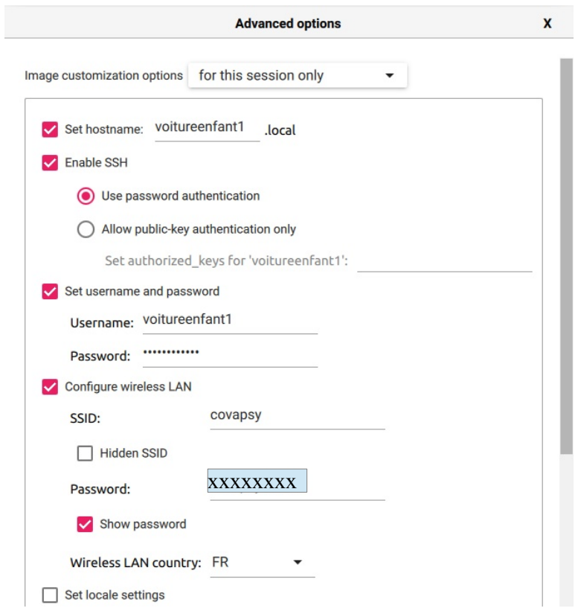
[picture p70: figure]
xxxxxxxx

Figure 2: paramètres de l'image Raspberry OS

Attention, le nano-ordinateur se trouvant connecté à Internet, il est nécessaire de ne

surtout pas laisser le login pi associé au mot de passe raspberry.

La configuration est terminée. Générer la carte (bouton Ecrire) et l’insérer dans la raspberry pi.

### 1.2 Recherche de l’IP du nano-ordinateur

Une fois ces configurations effectuées, le nano-ordinateur démarre. Pour s’y connecter à

distance, il est nécessaire d’avoir son adresse IP, adresse notée sous la forme de 4 nombres

192.168.1.4 par exemple (en IPv4).

Le PC doit être bien évidemment connecté sur le même réseau local.

- Une solution simple est de faire un ping avec une recherche DNS locale, depuis une

console (nommée invite de commande sous windows) avec le hostname défini dans la

partie précédente : ping voitureenfant1.local

Le nano-ordinateur répond alors avec son adresse IP.

Figure 3: Réponse à une recherche DNS locale

- Si le nano-ordinateur est connecté sur un réseau Ethernet filaire ou wifi avec

un serveur DHCP (c’est-à-dire qu’une machine, le routeur ou la box habituellement sur

les petits réseaux, distribue les adresses IP), on peut y trouver l’adresse IP du nano-

ordinateur. Pour cela, on se rend sur la page web de la box ou du routeur (la page web

de la box internet pour une utilisation à domicile, souvent accessible à l’adresse

192.168.1.1).

On présente ici les pages d’une LiveBox. Les routeurs grand public et les box ont la

même apparence avec une vue globale (overview) du réseau où on trouve les IP des

équipements connectés et des pages de configuration avancée (parfois nommées LAN

network), notamment pour la réservation des adresses IP.

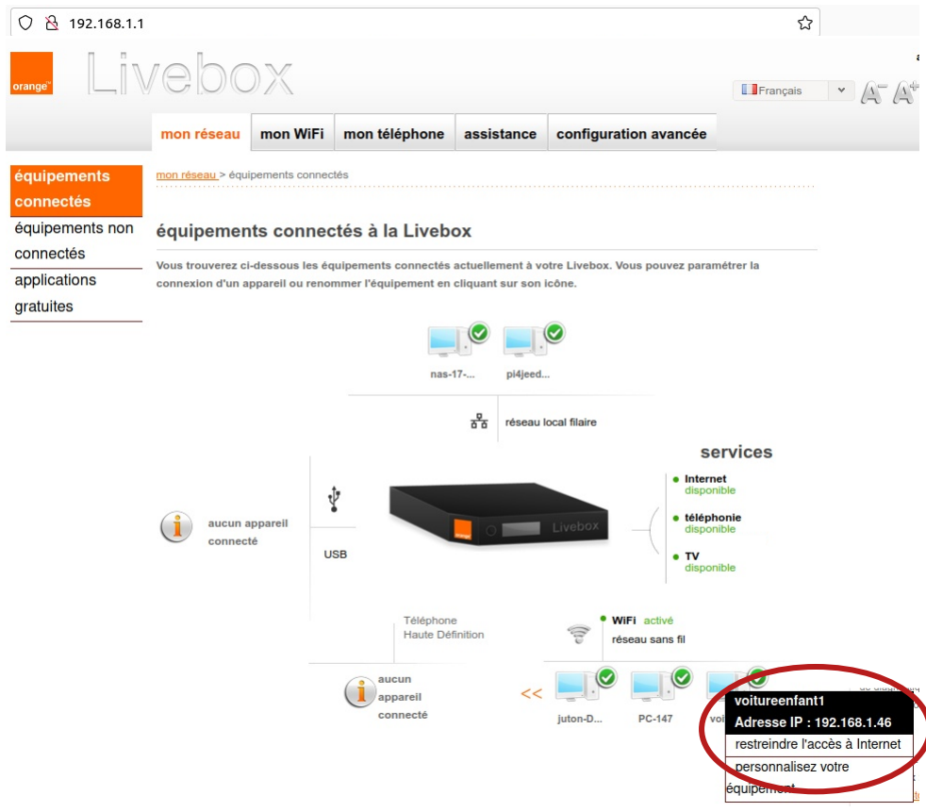
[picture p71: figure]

Figure 4: Présentation des équipements connectés au réseau par une LiveBox

Il est alors possible de réserver l’adresse IP dans le serveur DHCP, de sorte que le nano-

ordinateur obtienne toujours la même adresse lors de ces nouvelles connexions.

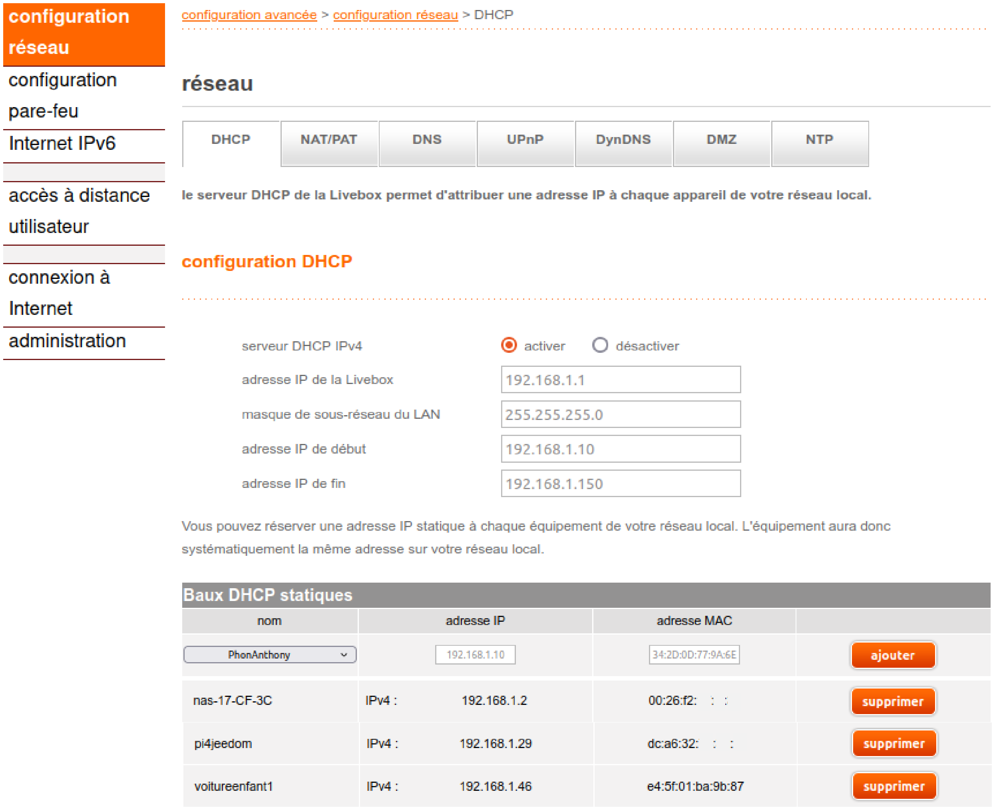
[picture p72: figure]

Figure 5: page de configuration DHCP d’une livebox où sont attribuées

les adresses IP statiques (ou IP réservées)

### 1.3 Connexion SSH

Une fois l’IP découverte, il est aisé de se connecter en SSH (Secure Shell). SSH est un protocole

de communication sécurisée permettant de dialoguer via une console du serveur SSH ouverte

sur le client SSH. Le nano-ordinateur est serveur SSH et le PC utilisateur est client SSH.

Très utile pour les accès à distance, le serveur SSH est installé par défaut sur les Raspberry Pi

(et il a été activé dans les options lors de la création de la carte SD).

Le client SSH est installé sur les PC Linux (et sans doute Mac). Sur les PC Windows, on peut

installer Putty par exemple.

Depuis une console (terminal Linux ou Putty sous Windows), on tape :

ssh login@<adresse IP de la raspberry pi>
L’authenticité de ce serveur SSH n’étant pas attesté, une demande de confirmation attend la

réponse yes, lors de la première connexion, puis le mot de passe de l’utilisateur.

Lorsque la connexion est réussie, le prompt indique :

le_nom_de_l_utilisateur@le_nom_de_la_machine, ici voitureenfant1@voitureenfant1

La commande exit permet de couper la connexion.

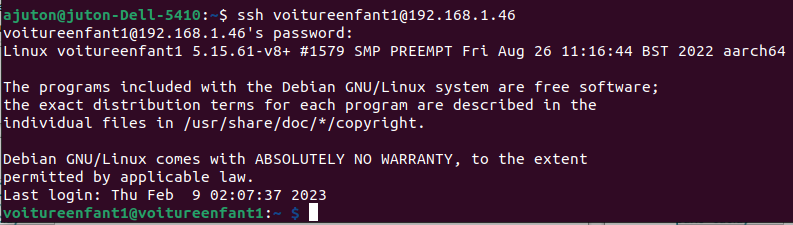
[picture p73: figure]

Figure 6: Connexion ssh à la Raspberry pi depuis un PC relié sur le même réseau local

## 2 Bureau à distance

Pour faciliter l’utilisation du nano-ordinateur, les outils graphiques sont plus accessibles que la

ligne de commande.

### 2.1 Mise en œuvre d’un bureau à distance VNC

VNC (Virtual Network Computing) est un protocole de bureau à distance. Le serveur VNC est la

Raspberry Pi et le client VNC est le PC utilisateur.

Le site raspberrypi.com propose là encore des solutions :

https://www.raspberrypi.com/documentation/computers/remote-access.html#virtual-network-

computing-vnc (https://www.raspberrypi.com/documentation/computers/remote-access.html#virtual-network-computing-vnc)

### 2.1.1 Installation du client sur le PC

Raspberry propose la solution gratuite mais propriétaire de RealVNC. Il est possible de

télécharger le client vnc (nommé VNC Viewer) : sur le site (https://www.realvnc.com/en/),

onglet Download, choisir la version adaptée de VNC Viewer à l’OS de l’ordinateur et l’installer.

### 2.1.2 Activation du serveur VNC sur le nano⁻ordinateur Raspberry Pi

Realvnc-vnc-serveur est installé avec l’image de Raspberry OS. Pour l’activer, utiliser la fenêtre

de configuration raspi-config, depuis l’accès SSH :

sudo raspi-config

Ensuite, choisir Interfacing Options > VNC › Yes.

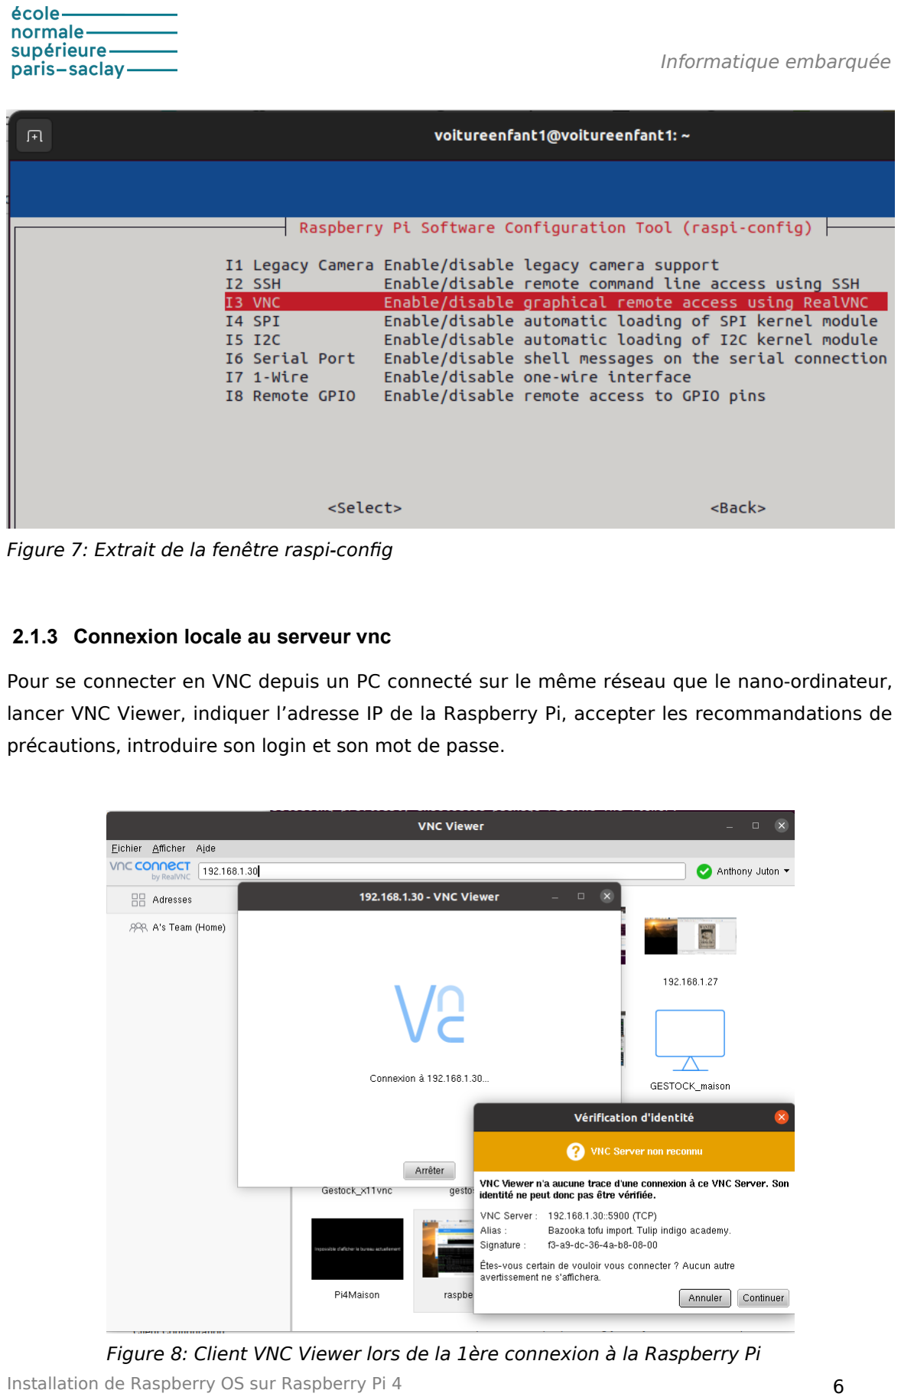
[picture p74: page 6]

Figure 7: Extrait de la fenêtre raspi-config

### 2.1.3 Connexion locale au serveur vnc

Pour se connecter en VNC depuis un PC connecté sur le même réseau que le nano-ordinateur,

lancer VNC Viewer, indiquer l’adresse IP de la Raspberry Pi, accepter les recommandations de

précautions, introduire son login et son mot de passe.

Figure 8: Client VNC Viewer lors de la 1ère connexion à la Raspberry Pi

On accède alors au bureau à distance, qui lors de la première connexion demande à faire

quelques mises à jour. Suite à un redémarrage on peut profiter du bureau à distance du nano-

ordinateur.

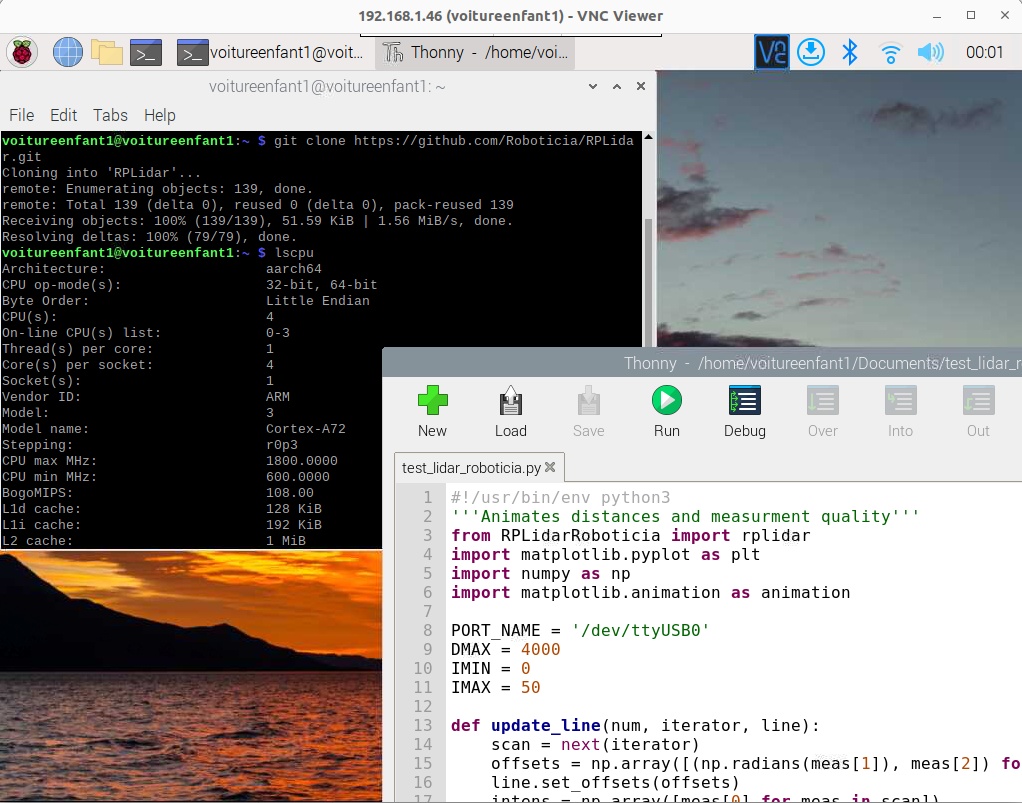
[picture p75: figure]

Figure 9: Bureau à distance de la Raspberry Pi via RealVNC

## 3 Remarques complémentaires

3.1 | Changement | de | la | résolution | du | bureau | à

distance

Pour plus de confort, il est possible d’augmenter la résolution du bureau à distance et

d’affecter plus de mémoire RAM au GPU, via la fenêtre Raspberry Pi Configuration accessible

depuis le menu principal (la framboise en haut à gauche)

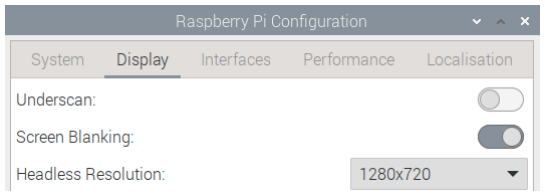
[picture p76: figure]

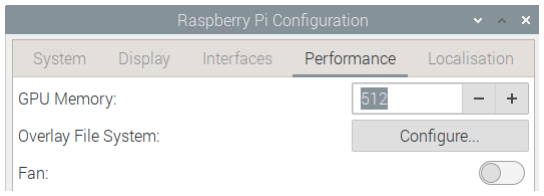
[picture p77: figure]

Figure 10: Extraits de la fenêtre Raspberry Pi Configuration

### 3.2 Imposer une adresse ip fixe

Pour permettre de se connecter à la Raspberry pi depuis son PC, même sans réseau accessible,

il est intéressant d’attribuer une IP fixe à la carte Ethernet (eth0), via le fichier dhcpd.conf

On ouvre le fichier en mode super-utilisateur depuis la console :

sudo nano /etc/dhcpcd.conf

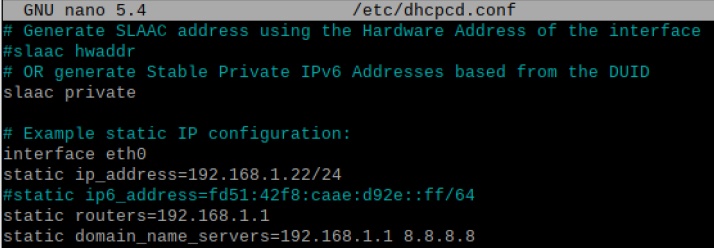
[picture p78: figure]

Attention à ne prendre que des adresses IP privées (non attribuées à des usages publics). Les

adresses de type 192.168.x.y sont des adresses privées.

## 4 Utiliser les entrées/sorties

Pour utiliser les entrées/sorties et les communications, il faut les activer via la fenêtre

Raspberry Pi Configuration.

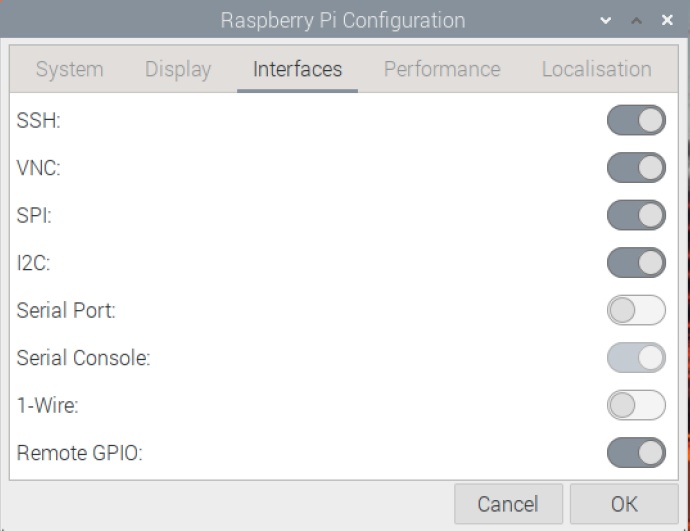
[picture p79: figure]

Plus d’infos sur https://gpiozero.readthedocs.io/en/stable/installing.html

### 4.1 Installation des paquets utiles

Pour le bon fonctionnement de la voiture, quelques paquets Linux sont utiles. Ils seront

présentés plus loin.

Depuis la console, lancer les commandes d’installation suivantes :

- sudo apt update
- sudo apt upgrade
- sudo apt-get install libatlas-base-dev
- pip install matplotlib
- pip install numpy -⁻upgrade
- sudo pip install rpi-hardware-pwm
- sudo apt-get install joystick
- pip install pyPS4Controller
- pip install rplidar-roboticia
- sudo apt install python3-gpiozero

### 4.2 Les PWM matérielles

Pour la commande des moteurs, on utilise les pwm hardware, plus précises que les pwm

software. Les informations détaillées sont sur https://pypi.org/project/rpi-hardware-pwm/

On ajoute l’activation des pwm (dtoverlay=pwm-2chan,pin=12,func=4,pin2=13,func2=4) à

config.txt :

Figure 11: Activation des entrées/sorties via Raspberry Pi

Configuration

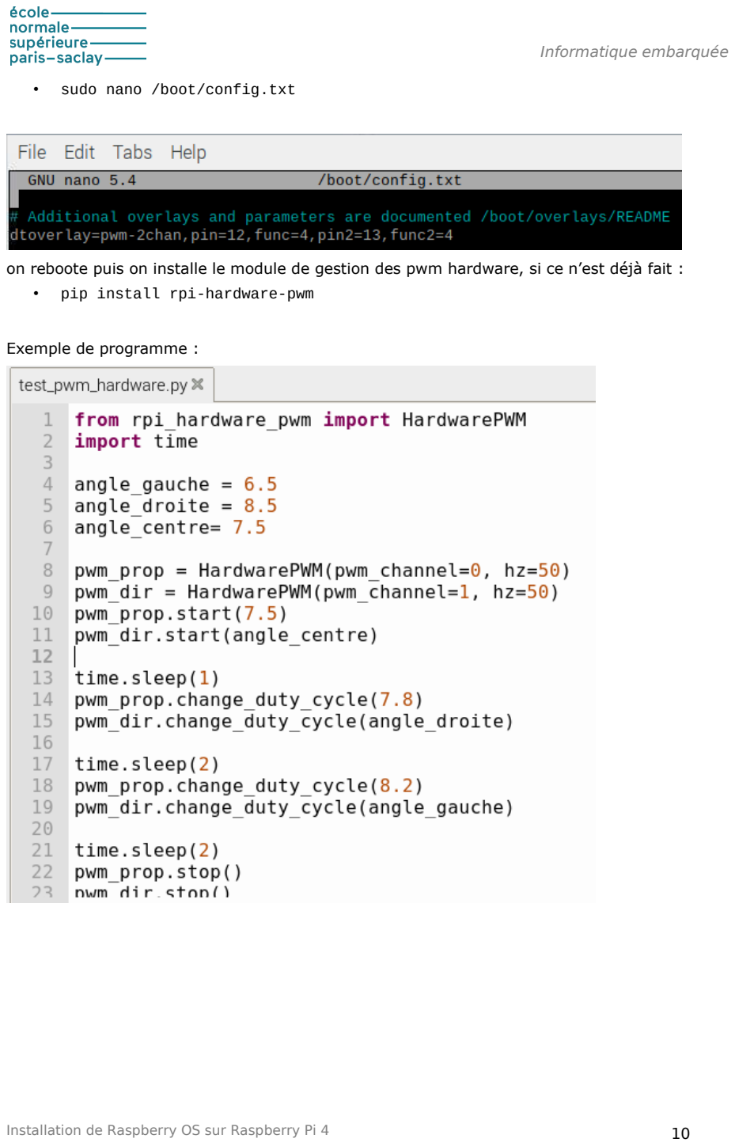
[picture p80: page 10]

- sudo nano /boot/config.txt

on reboote puis on installe le module de gestion des pwm hardware, si ce n’est déjà fait :

- pip install rpi-hardware-pwm

Exemple de programme :

## 5 Le Lidar

La bibliothèque semblant la plus intéressante, notamment pour la prise en compte du mode

ExpressScan est la suivante : https://github.com/Roboticia/RPLidar/

Le module python s’installe de la manière suivante, si ce n’est déjà fait :

- $ pip install rplidar-roboticia

Le programme suivant permet de remettre le lidar à zéro, quelque soit la coupure du

programme précédent.

Attention : il faut préciser le baudrate : la version A2M8 (noir et rouge) du RPLidar utilise une

communication à 115200 baud et la version A2M12 (noir et violet) une communication à

256000 baud.

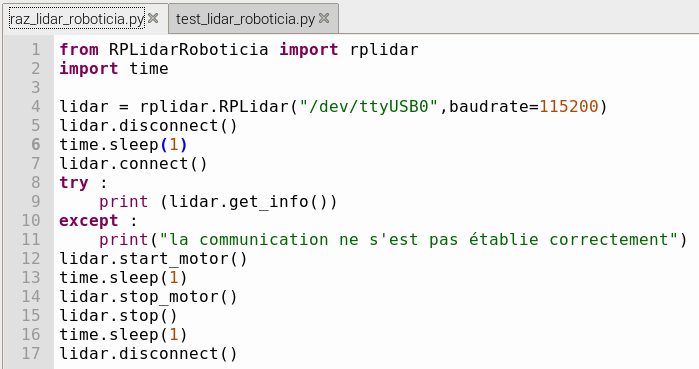
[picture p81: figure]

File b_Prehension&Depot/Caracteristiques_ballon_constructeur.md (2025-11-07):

Lien vers le site web du concours Float Lift and Fly : 
https://www.youtube.com/watch?v=wIxYmsmQtH4    
;     https://www.planete-sciences.org/espace/Float-Lift-Fly-Contest/Le-concours

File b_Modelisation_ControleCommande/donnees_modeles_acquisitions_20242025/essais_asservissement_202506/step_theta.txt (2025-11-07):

0.363969087600708	-1	[3.079322191501172, 10.629343122949068, 4.73693784778728, 188.75, 0.375, 10.6875]
0.765815019607544	-1	[3.9189617377272716, 10.974194552053035, 4.76318537008955, 189.25, 0.1875, 9.0625]
1.178894281387329	-1	[3.9189617377272716, 10.974194552053035, 4.817233198529093, 189.1875, 0.8125, 8.5]
1.5972328186035156	-1	[3.0835902324141857, 10.635582281137557, 4.793872521237213, 188.25, 1.8125, 8.6875]
2.002089023590088	-1	[2.7292384387684727, 11.021475589203186, 4.802144407583048, 186.25, 2.75, 9.625]
2.417708158493042	-1	[2.7292384387684727, 11.021475589203186, 4.80435286096917, 183.1875, 3.0625, 10.25]
2.8409035205841064	-1	[1.7080356128885152, 9.826169357519463, 4.777408116804671, 178.6875, 2.875, 10.0625]
3.2635836601257324	-1	[1.7080356128885152, 9.826169357519463, 4.828365375825624, 172.9375, 2.125, 9.1875]
3.670126438140869	-1	[1.7080356128885152, 9.826169357519463, 4.814384175385685, 166.125, 1.3125, 8.75]
4.0782787799835205	-1	[1.7080356128885152, 9.826169357519463, 4.8018678563066, 158.875, 0.875, 9.125]
4.478981971740723	-1	[1.7080356128885152, 9.826169357519463, 4.782139303483921, 150.625, 0.9375, 10.125]
4.9053239822387695	-1	[1.7080356128885152, 9.826169357519463, 4.75513482115129, 141.625, 1.1875, 10.75]
5.31121039390564	-1	[1.7080356128885152, 9.826169357519463, 4.727140978395243, 131.25, 1.6875, 10.5]
5.727679491043091	-1	[2.2130768638577605, 11.504932985364476, 4.693983573573323, 120.375, 2.125, 9.75]
6.132441282272339	-1	[2.2130768638577605, 11.504932985364476, 4.667277123257692, 108.0, 2.4375, 9.3125]
6.561050891876221	-1	[2.2130768638577605, 11.504932985364476, 4.63523981040169, 95.5, 2.25, 9.625]
6.99081563949585	-1	[1.4227564339585774, 12.500320666065399, 4.590495939346503, 81.625, 1.625, 10.3125]
7.397703170776367	-1	[-0.03247970459532468, 13.786447703835146, 4.559530203926748, 66.625, 0.8125, 10.5625]
7.807633876800537	-1	[-0.03247970459532468, 13.786447703835146, 4.513490936771372, 51.625, 0.4375, 10.25]
8.21845817565918	-1	[0.9234982300051674, 9.817465298898835, 4.466191950486804, 36.4375, 0.625, 10.0]
8.631540298461914	-1	[0.3348454538459501, 11.893880602355518, 4.403744678280311, 20.375, 1.0625, 10.25]
9.044808864593506	-1	[0.3348454538459501, 11.893880602355518, 4.337732277972765, 4.0, 1.5625, 10.8125]
9.456551551818848	-1	[1.8194384979292233, 11.353573221177255, 4.266561291646327, 346.75, 1.625, -5.875]
9.860717535018921	-1	[1.8194384979292233, 11.353573221177255, 4.2206338979077165, 329.9375, 1.625, 10.625]
10.308172225952148	-1	[1.8194384979292233, 11.353573221177255, 4.168599928892383, 312.3125, 1.375, 9.875]
10.718757629394531	0	[1.8194384979292233, 11.353573221177255, 4.122528391265311, 293.0625, 1.125, 9.5]
11.149764060974121	0	[1.5122524695616344, 11.805381068923749, 4.05881577826723, 275.0, 1.0625, 10.0]
11.5838303565979	0	[1.7967091876068735, 11.87427234513995, 3.971293606249203, 256.6875, 1.4375, -5.8125]
12.010698318481445	0	[1.7967091876068735, 11.87427234513995, 3.915076266656823, 238.8125, 2.125, -5.375]
12.436789751052856	0	[1.8627502159453677, 11.57581982506491, 3.8197167682408004, 221.75, 2.9375, 10.75]
12.85739278793335	0	[1.7891623795215699, 11.690138462818485, 3.745491557404222, 204.5625, 3.8125, 9.75]
13.284133195877075	0	[1.7891623795215699, 11.690138462818485, 3.677065993659556, 188.1875, 4.3125, 9.3125]
13.709223508834839	0	[1.7301730718511046, 12.184067320623859, 3.6049374596338093, 172.1875, 4.125, 9.8125]
14.125921726226807	0	[1.720471740327672, 12.294849379726262, 3.5438814360342663, 156.6875, 3.1875, 10.5]
14.54366660118103	0	[1.720471740327672, 12.294849379726262, 3.497750103903506, 141.5625, 2.1875, 10.4375]
14.961072444915771	0	[1.3169339719753117, 12.493145099624131, 3.412063259196096, 127.125, 1.625, 10.125]
15.402859926223755	0	[1.2360026196068785, 12.439674156787817, 3.3331694928048656, 112.75, 1.875, 10.0]
15.8143630027771	0	[1.2360026196068785, 12.439674156787817, 3.237991881567797, 98.1875, 2.6875, 10.5625]
16.22792887687683	0	[1.354544894977682, 12.281277004364348, 3.1362737801360434, 85.0, 3.4375, -5.875]
16.64323353767395	0	[1.259048660304241, 12.531808415368944, 3.0659647589079224, 72.0625, 3.8125, -5.875]
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

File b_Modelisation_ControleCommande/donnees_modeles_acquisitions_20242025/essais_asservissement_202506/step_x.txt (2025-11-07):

0.3561899662017822	50	[2.3848679617112296, 1.7650281032998372, 1.7802492650902606, 82.0625, 2.5, 8.4375]
0.7559504508972168	50	[2.401545989883981, 1.7638087931520303, 1.779298536352432, 81.1875, 2.5, 8.75]
1.1572015285491943	50	[2.640010048582986, 1.5125573082457464, 1.7628592992999443, 80.8125, 2.0625, 10.6875]
1.5520665645599365	50	[2.640010048582986, 1.5125573082457464, 1.7629102637857703, 80.4375, 1.0625, -4.875]
1.9478662014007568	50	[2.3764677291870755, 1.866507623903292, 1.7505570366458425, 79.9375, -0.0625, -5.5]
2.3530569076538086	50	[2.234849584481068, 2.114230896999737, 1.7478212643199909, 79.375, -0.875, 9.6875]
2.7503795623779297	50	[2.234849584481068, 2.114230896999737, 1.7317575374391772, 78.9375, -0.9375, 8.5]
3.1523072719573975	50	[2.266970499183628, 2.253821555559147, 1.7203082195837387, 78.75, -0.25, 9.0625]
3.579334259033203	50	[2.360747588974396, 2.217661731043434, 1.693471896204171, 78.75, 0.75, 10.9375]
3.979501485824585	50	[2.360747588974396, 2.217661731043434, 1.6735328568239638, 78.6875, 1.75, -4.8125]
4.377819538116455	50	[2.3432107568188787, 2.370476017123024, 1.6610076857977003, 78.5, 2.0625, -5.375]
4.7810468673706055	50	[2.328071965060274, 2.467644055730189, 1.6474012564773601, 78.25, 1.625, 9.875]
5.187668323516846	50	[2.328071965060274, 2.467644055730189, 1.6511620993242124, 78.1875, 0.6875, 8.875]
5.587143659591675	50	[2.3183329029246997, 2.781043407919632, 1.6489065543308155, 78.1875, -0.1875, 9.625]
5.987004518508911	50	[2.277212346441226, 2.9655722867805205, 1.6311761912019846, 78.1875, -0.8125, -5.625]
6.386892080307007	50	[2.277212346441226, 2.9655722867805205, 1.6248566826709199, 78.25, -0.8125, -4.75]
6.78367280960083	50	[2.2253888702079516, 3.2977868509805637, 1.612851673481076, 78.3125, -0.3125, -5.3125]
7.210511922836304	50	[2.5688313986268905, 3.2215830040429334, 1.5979384572255704, 78.375, 0.5, 10.0]
7.613279342651367	50	[2.5688313986268905, 3.2215830040429334, 1.5806099779923477, 78.625, 1.4375, 9.0625]
8.013283967971802	50	[2.3287791036709713, 3.991805269416065, 1.5680597329535713, 79.125, 1.8125, 9.8125]
8.42379379272461	50	[2.662439899952634, 4.21445061455183, 1.5517767420514852, 79.8125, 1.75, -5.5625]
8.865889072418213	50	[2.662439899952634, 4.21445061455183, 1.5553919829679652, 80.5, 1.0625, -4.75]
9.276417016983032	50	[2.112221819022551, 4.575567611543246, 1.5426123022713423, 81.375, 0.0, -5.5625]
9.673927068710327	50	[2.414255338047135, 5.017113477066126, 1.5482605311186113, 82.3125, -0.6875, 10.0]
10.092541217803955	50	[2.414255338047135, 5.017113477066126, 1.5398567940588246, 83.5625, -0.875, 9.5]
10.506646156311035	0	[2.1539160941587006, 5.436395528566195, 1.5267805754460064, 85.125, -0.4375, 10.5]
10.923423051834106	0	[2.1564297212006993, 5.662776543861135, 1.5135543677038572, 86.875, 0.75, -5.375]
11.348766565322876	0	[2.1564297212006993, 5.662776543861135, 1.4926140812858062, 88.75, 2.375, -5.375]
11.755277395248413	0	[2.1691242553261403, 6.226923474057644, 1.4742954587246975, 90.8125, 3.875, 10.375]
12.151351928710938	0	[2.197698239341452, 6.472662498470667, 1.4669675510514906, 92.9375, 4.4375, 9.1875]
12.565502405166626	0	[2.197698239341452, 6.472662498470667, 1.4577644604847666, 95.3125, 4.0625, 9.1875]
12.991402387619019	0	[2.1576000946421128, 6.999267336602306, 1.4458943274997802, 98.0625, 2.875, 10.4375]
13.402456045150757	0	[2.2083467721470154, 7.334202350362449, 1.4442456540922561, 101.1875, 1.375, -5.3125]
13.827186584472656	0	[2.2083467721470154, 7.334202350362449, 1.4340183967691134, 104.25, 0.5, -5.5]
14.271294832229614	0	[2.2562170157705093, 7.837068889610047, 1.4092049630578545, 107.625, 0.3125, 10.0625]
14.66348123550415	0	[2.4218836992959436, 8.106837289429668, 1.392250036204753, 111.625, 1.0625, 8.9375]
15.058102130889893	0	[2.4218836992959436, 8.106837289429668, 1.3611866674738635, 115.6875, 2.1875, 9.125]
15.481428861618042	0	[2.4218836992959436, 8.106837289429668, 1.327148701741932, 120.1875, 3.25, 10.25]
15.878031730651855	0	[2.2731824351344065, 8.891777392610644, 1.2918882706888082, 125.5625, 3.8125, -5.75]
16.28940486907959	0	[2.2731824351344065, 8.891777392610644, 1.272044541398793, 130.875, 3.4375, -5.9375]
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

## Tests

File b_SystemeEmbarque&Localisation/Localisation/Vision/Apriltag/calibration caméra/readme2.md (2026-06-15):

La calibration de la caméra est automatisée. capture_automatique_photos_calibration_2026.py prend 30 photos avec un intervalle de 5 secondes, 
toutes utilisables pour la calibration (celles qui ne sont pas valides sont rejetées). En lançant le programme coeff_calibration_2026.py, les photos sont immédiatement récupérées et les coefficients de calibrations sont renvoyés.

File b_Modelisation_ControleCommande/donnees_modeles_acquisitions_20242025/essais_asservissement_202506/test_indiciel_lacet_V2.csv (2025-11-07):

0,0785977840423584 | +AC0-20 | 0
0,20234489440918 | +AC0-20 | 0,280462941227285 | 0,123747110366821
0,323304891586304 | +AC0-20 | 1,35232044946457 | 0,120959997177124
0,442130565643311 | +AC0-20 | 1,65020345027 | 0,118825674057007
0,556218147277832 | +AC0-20 | 2,44557364523871 | 0,114087581634521
0,669443368911743 | +AC0-20 | 2,71621329202915 | 0,113225221633911
0,789738416671753 | +AC0-20 | 4,0901270792429 | 0,12029504776001
0,928462505340576 | +AC0-20 | 4,08342140002929 | 0,138724088668823
1,04752278327942 | +AC0-20 | 5,13477462016513 | 0,119060277938843
1,17654466629028 | +AC0-20 | 5,55244555206338 | 0,129021883010864
1,30504560470581 | +AC0-20 | 5,78868165782552 | 0,128500938415527
1,43767213821411 | +AC0-20 | 6,26706277268372 | 0,132626533508301
1,56046366691589 | +AC0-20 | 6,46576127827748 | 0,122791528701782
1,69699239730835 | +AC0-20 | 6,36057359363883 | 0,136528730392456
1,83323431015015 | +AC0-20 | 5,39515879411962 | 0,136241912841797
1,94652056694031 | +AC0-20 | 5,39515879411962 | 0,113286256790161
2,07630658149719 | +AC0-20 | 5,39515879411962 | 0,129786014556885
2,21069741249084 | +AC0-20 | 5,39515879411962 | 0,134390830993652
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

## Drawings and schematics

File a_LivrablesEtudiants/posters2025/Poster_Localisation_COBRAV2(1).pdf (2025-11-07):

## Défi CoBRA

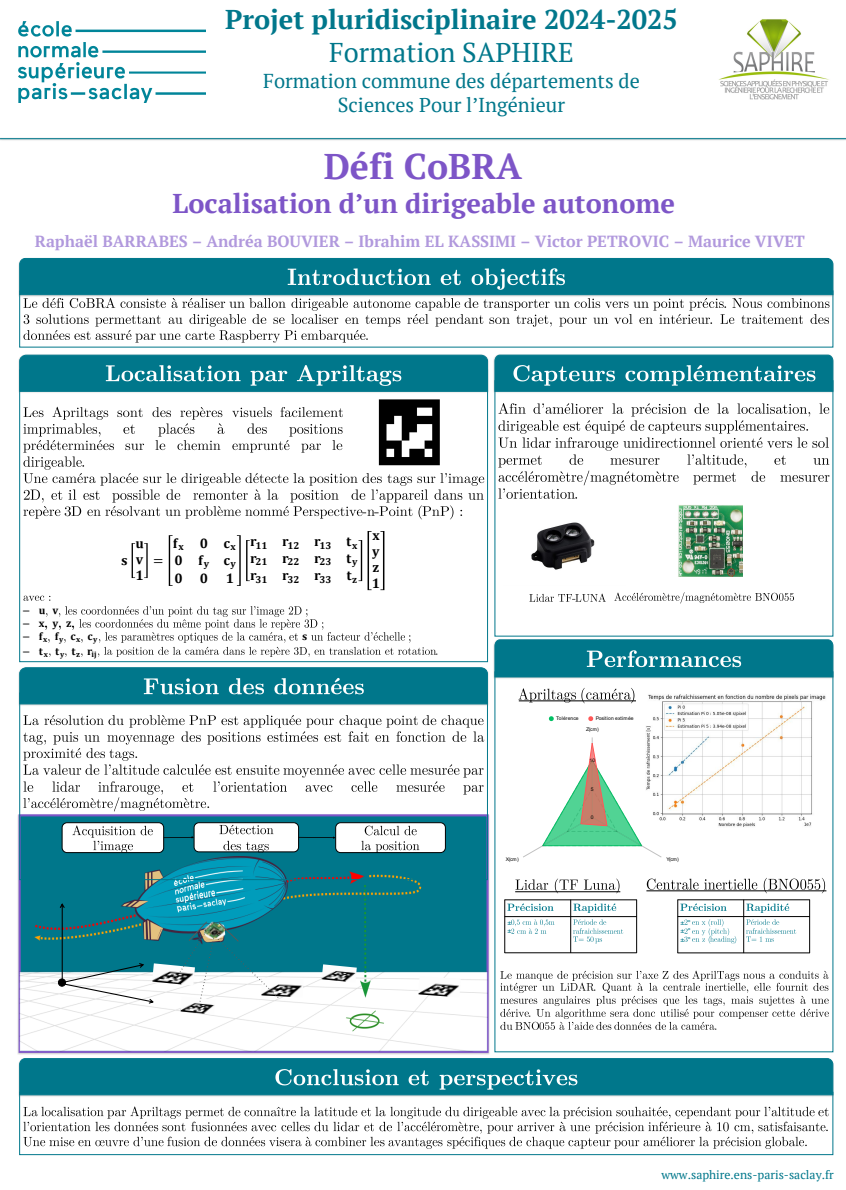
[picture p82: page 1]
tz rij

Projet pluridisciplinaire 2024-2025
Formation SAPHIRE
Formation commune des départements de
Sciences Pour l’Ingénieur

Localisation d’un dirigeable autonome

Raphaël BARRABES – Andréa BOUVIER – Ibrahim EL KASSIMI – Victor PETROVIC – Maurice VIVET

www.saphire.ens-paris-saclay.fr

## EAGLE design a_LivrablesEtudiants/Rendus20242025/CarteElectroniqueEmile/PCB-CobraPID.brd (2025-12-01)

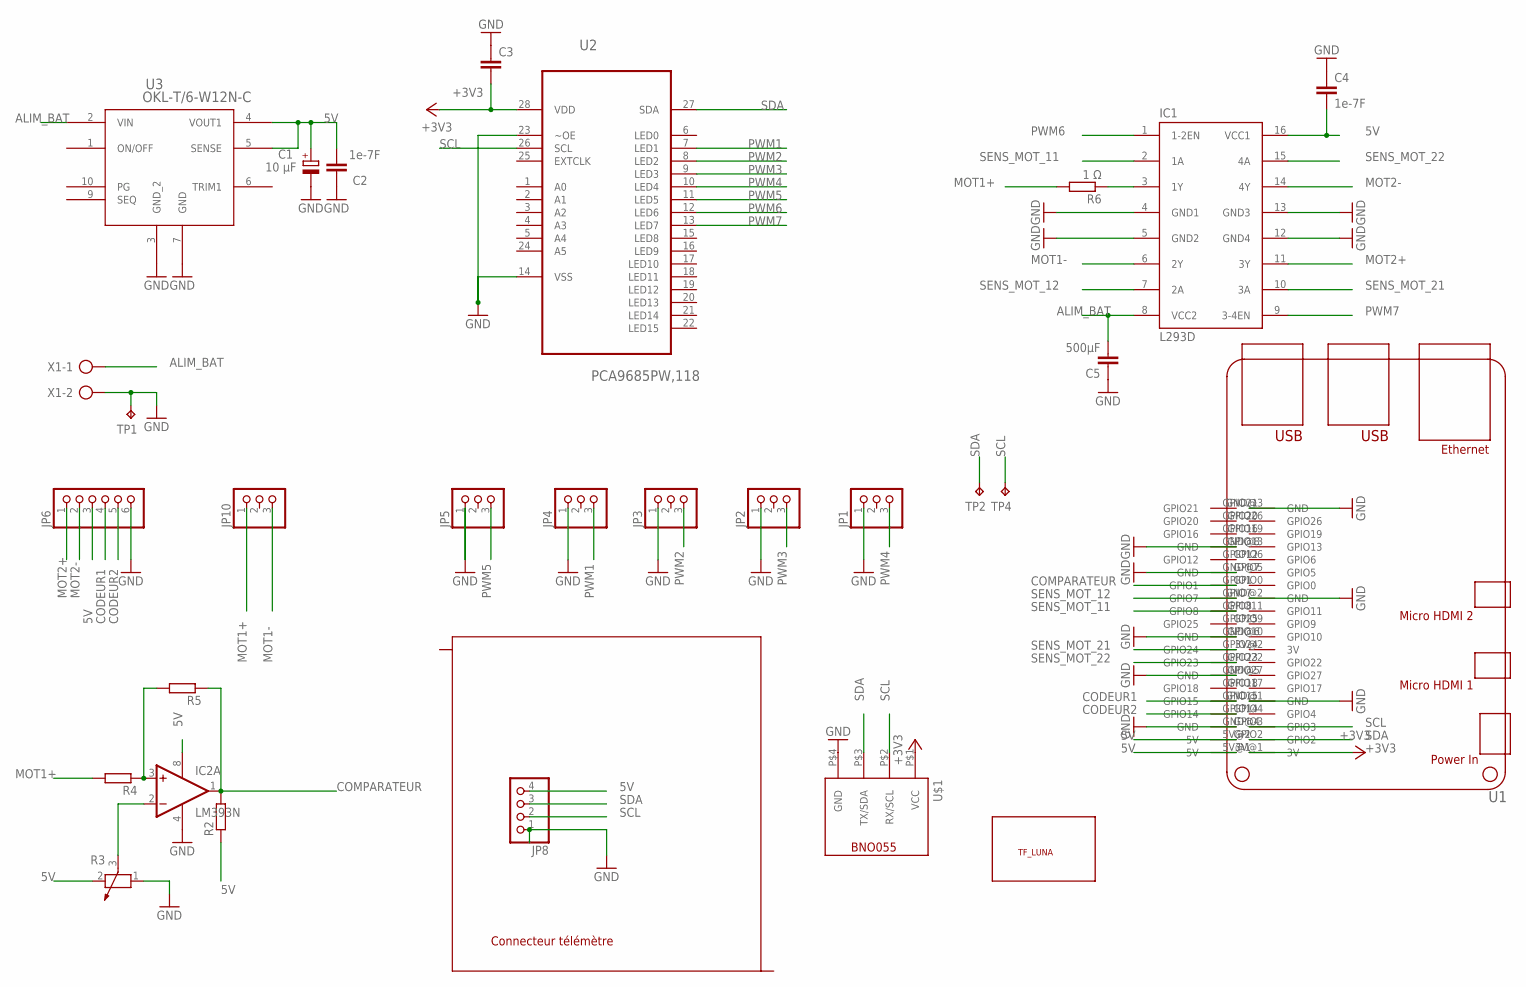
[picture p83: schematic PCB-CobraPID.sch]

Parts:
C1: 10 μF; E5-10,5
C2, C4: 1e-7F; C1206
C3: C-EUC1206; C1206
C5: 500μF; C1206
IC1: L293D; DIL16
IC2: LM393N; DIL08
JP1, JP2, JP3, JP4, JP5, JP10: PINHD-1X3/90; 1X03/90
JP6: PINHD-1X6/90; 1X06/90
JP8: PINHD-1X4; 1X04
R2, R4, R5: R-EU_R1206; R1206
R3: POTENTIOMETER_PT-10; PT-10
R6: 1 Ω; R1206
TP1, TP2, TP4: TPPAD1-17; P1-17
U1: RPI5
U2: PCA9685PW,118; SOP65P640X110-28N
U3: OKL-T/6-W12N-C; OKL-T/6-W12N-C_MUR
U$1: MODULE_BNO055
U$2: TF_LUNA
X1: AK500/2

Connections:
5V: C1.+, C2.2, C4.2, IC1.16 (VCC1), IC2.8 (V+), JP6.3, JP8.4, R2.1, R3.2, U1.5V@1 (5V), U1.5V@2 (5V), U3.4 (VOUT1), U3.5 (SENSE)
+3V3: C3.2, U1.3V@1 (3V), U2.28 (VDD), U$1.P$1 (VCC)
ALIM_BAT: C5.2, IC1.8 (VCC2), U3.2 (VIN), X1.1
CODEUR1: JP6.4, U1.GPIO15
CODEUR2: JP6.5, U1.GPIO14
COMPARATEUR: IC2.1 (OUT), R2.2, R5.1, U1.GPIO1
GND: C1.-, C2.1, C3.1, C4.1, C5.1, IC1.4 (GND1), IC1.5 (GND2), IC1.12 (GND4), IC1.13 (GND3), IC2.4 (V-), JP1.1, JP2.1, JP3.1, JP4.1, JP6.6, JP8.1, R3.1, TP1.TP, U1.GND@1 (GND), U1.GND@2 (GND), U1.GND@3 (GND), U1.GND@4 (GND), U1.GND@5 (GND), U1.GND@6 (GND), U1.GND@7 (GND), U1.GND@8 (GND), U2.14 (VSS), U2.23 (~OE), U3.3 (GND_2), U3.7 (GND), U$1.P$4 (GND), X1.2
GND1: JP5.1
MOT1+: JP10.1, R4.2, R6.2
MOT1-: IC1.6 (2Y), JP10.3
MOT2+: IC1.11 (3Y), JP6.1
MOT2-: IC1.14 (4Y), JP6.2
unnamed: IC2.3 (+IN), R4.1, R5.2
unnamed: IC2.2 (-IN), R3.3
unnamed: IC1.3 (1Y), R6.1
PWM1: JP4.3, U2.7 (LED1)
PWM2: JP3.3, U2.8 (LED2)
PWM3: JP2.3, U2.9 (LED3)
PWM4: JP1.3, U2.10 (LED4)
PWM5: JP5.3, U2.11 (LED5)
PWM6: IC1.1 (1-2EN), U2.12 (LED6)
PWM7: IC1.9 (3-4EN), U2.13 (LED7)
SCL: JP8.2, TP4.TP, U1.GPIO3, U2.26 (SCL), U$1.P$2 (RX/SCL)
SDA: JP8.3, TP2.TP, U1.GPIO2, U2.27 (SDA), U$1.P$3 (TX/SDA)
SENS_MOT_11: IC1.2 (1A), U1.GPIO8
SENS_MOT_12: IC1.7 (2A), U1.GPIO7
SENS_MOT_21: IC1.10 (3A), U1.GPIO24
SENS_MOT_22: IC1.15 (4A), U1.GPIO23

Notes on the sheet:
Connecteur télémètre

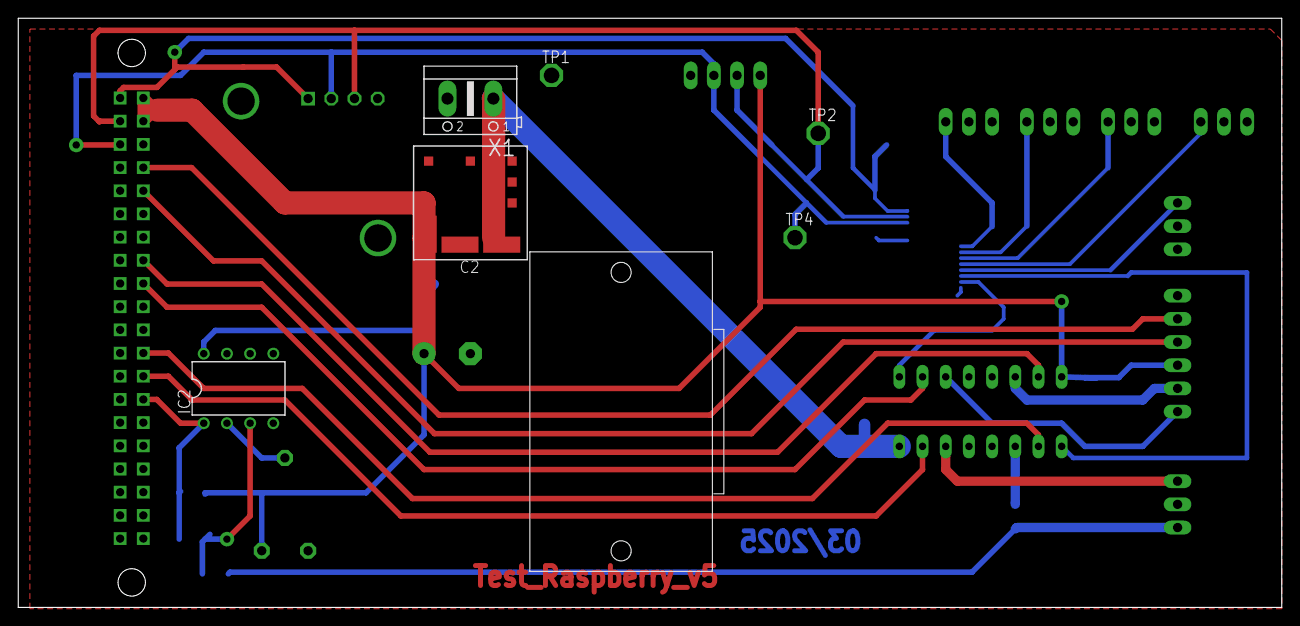
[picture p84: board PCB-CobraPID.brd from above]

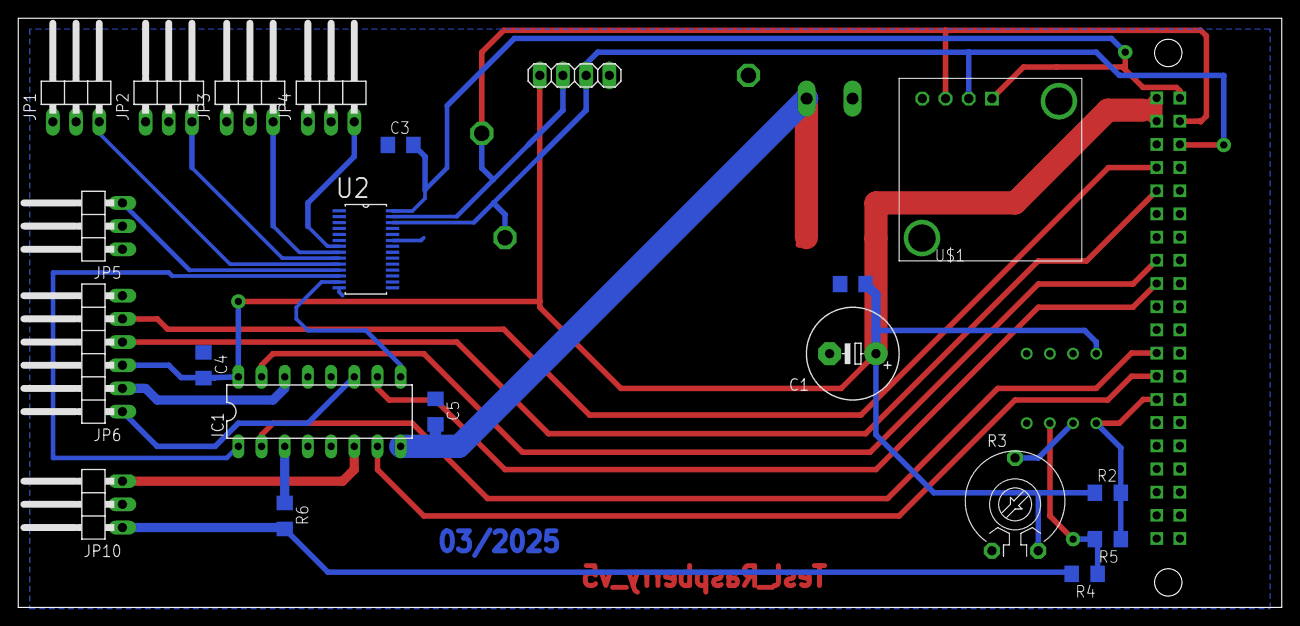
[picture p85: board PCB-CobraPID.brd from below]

Board: 2 copper layers, 138.4 x 64.5 mm, 29 parts (21 on the bottom side), 27 nets.

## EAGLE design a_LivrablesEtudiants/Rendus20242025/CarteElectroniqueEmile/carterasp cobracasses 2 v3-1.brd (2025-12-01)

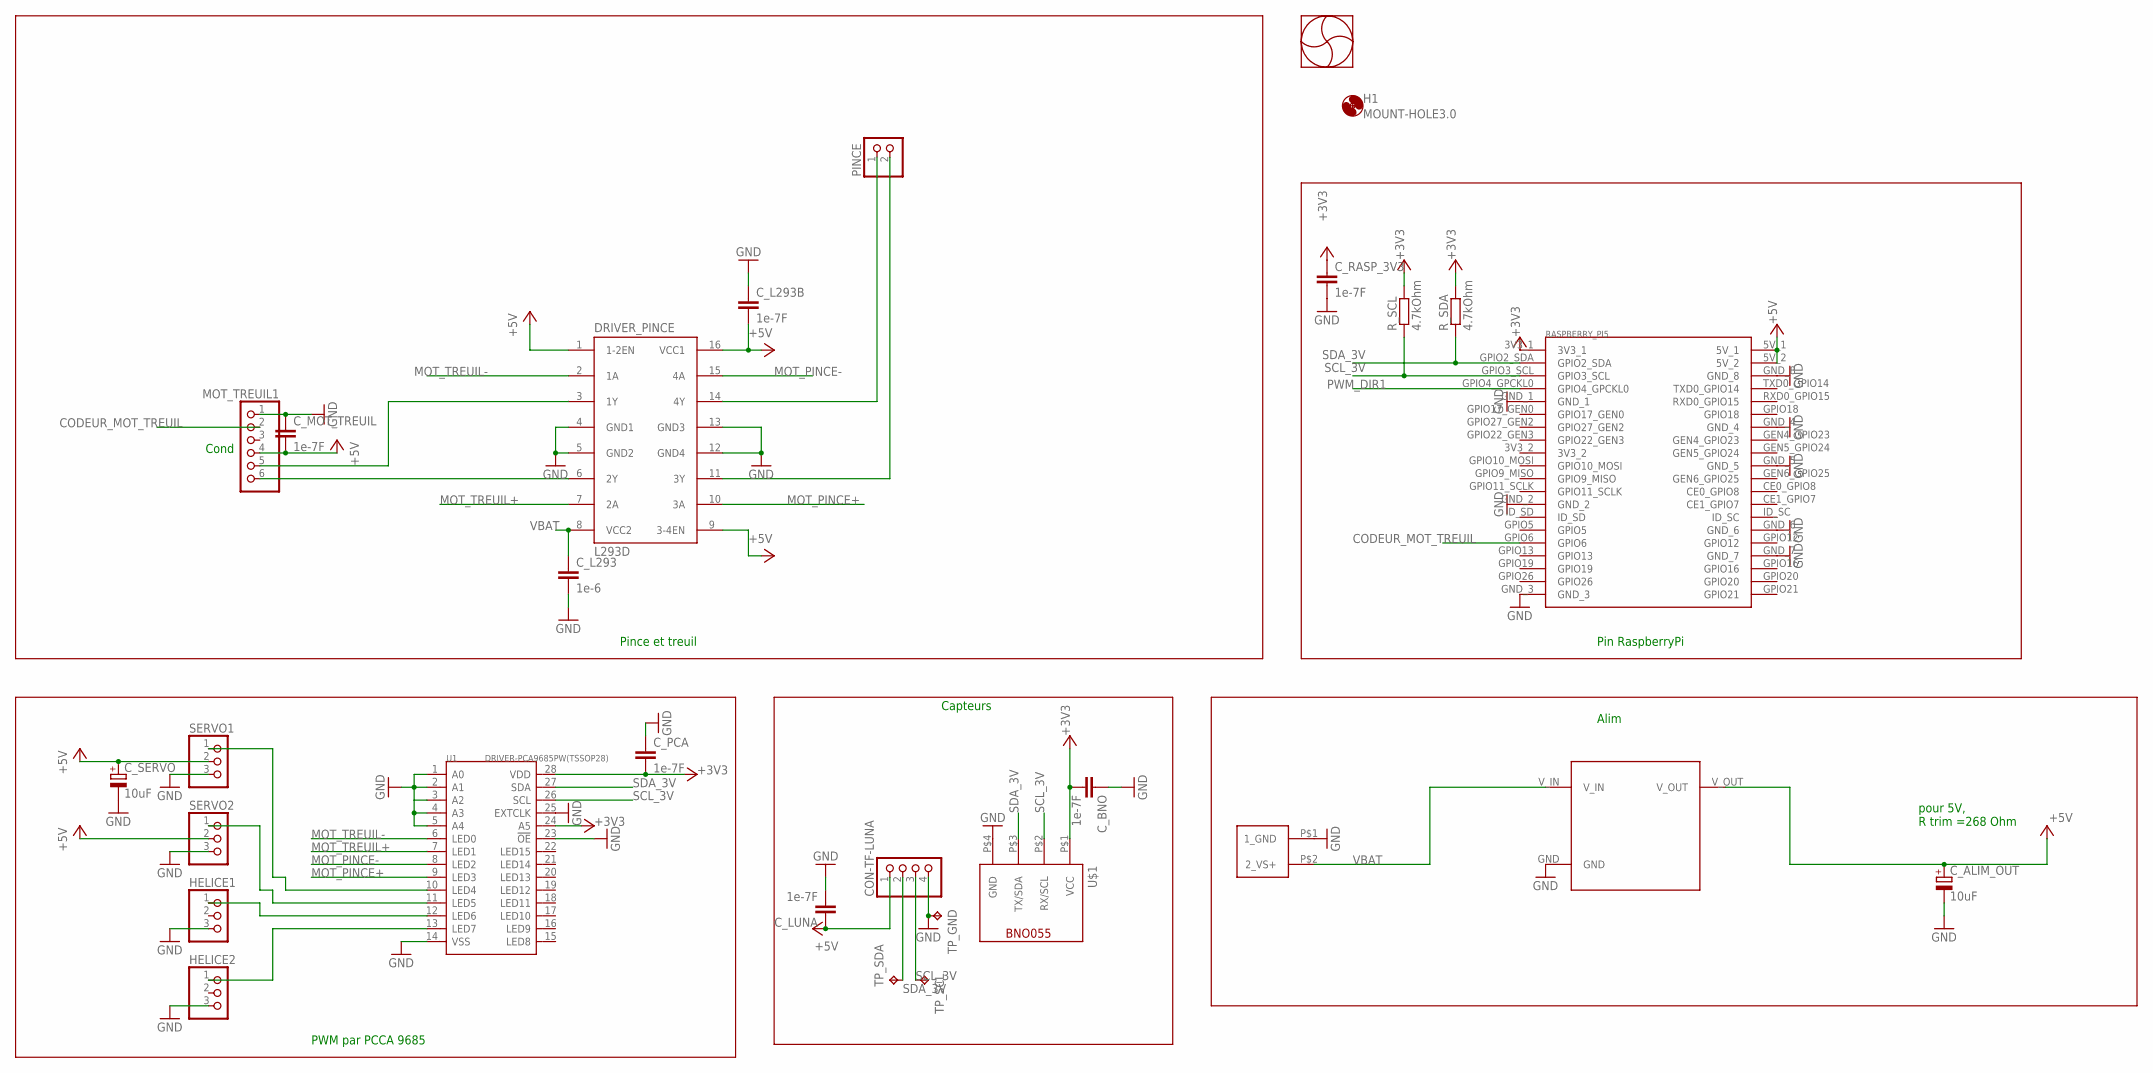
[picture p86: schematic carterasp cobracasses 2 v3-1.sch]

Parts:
CON-TF-LUNA: PINHD-1X4; 1X04
C_ALIM_OUT: 10uF; E5-8,5
C_BNO: 1e-7F; C1206
C_L293: 1e-6; C1206
C_L293B: 1e-7F; C1206
C_LUNA: 1e-7F; C1206
C_MOT_TREUIL: 1e-7F; C1206
C_PCA: 1e-7F; C1206
C_RASP_3V3: 1e-7F; C1206
C_SERVO: 10uF; E5-8,5
DRIVER_PINCE: L293D; DIL16
H1: MOUNT-HOLE3.0; 3,0
HELICE1, HELICE2: PINHD-1X3; 1X03
MOT_TREUIL1: PINHD-1X6; 1X06
PINCE: PINHD-1X2; 1X02
R_SCL: 4.7kOhm; R0805
R_SDA: 4.7kOhm; R0805
SERVO1, SERVO2: PINHD-1X3; 1X03
TP_GND: TPPAD1-13; P1-13
TP_SCL: TPPAD1-13; P1-13
TP_SDA: TPPAD1-13; P1-13
U1: DRIVER-PCA9685PW(TSSOP28); TSSOP28-0.65-9.7X4.4MM
U$1: MODULE_BNO055
U$2: CONN_ALIM
U$3: RASPBERRY_PI5; RP5
U$4: OKL_T6_W12
U$5: VENTILLATEUR_RASP

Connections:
+3V3: C_BNO.2, C_PCA.2, C_RASP_3V3.1, R_SCL.2, R_SDA.2, U1.24 (A5), U1.28 (VDD), U$1.P$1 (VCC), U$3.3V3_1
+5V: CON-TF-LUNA.1, C_ALIM_OUT.+, C_L293B.2, C_LUNA.1, C_MOT_TREUIL.2, C_SERVO.+, DRIVER_PINCE.1 (1-2EN), DRIVER_PINCE.9 (3-4EN), DRIVER_PINCE.16 (VCC1), MOT_TREUIL1.4, SERVO1.2, SERVO2.2, U$3.5V_1, U$3.5V_2, U$4.V_OUT
CODEUR_MOT_TREUIL: MOT_TREUIL1.2, U$3.GPIO6
GND: CON-TF-LUNA.4, C_ALIM_OUT.-, C_BNO.1, C_L293.2, C_L293B.1, C_LUNA.2, C_MOT_TREUIL.1, C_PCA.1, C_RASP_3V3.2, C_SERVO.-, DRIVER_PINCE.4 (GND1), DRIVER_PINCE.5 (GND2), DRIVER_PINCE.12 (GND4), DRIVER_PINCE.13 (GND3), HELICE1.3, HELICE2.3, MOT_TREUIL1.1, SERVO1.3, SERVO2.3, TP_GND.TP, U1.1 (A0), U1.2 (A1), U1.3 (A2), U1.4 (A3), U1.5 (A4), U1.14 (VSS), U1.23 (!OE), U1.25 (EXTCLK), U$1.P$4 (GND), U$2.P$1 (1_GND), U$3.GND_1, U$3.GND_2, U$3.GND_3, U$3.GND_4, U$3.GND_5, U$3.GND_6, U$3.GND_7, U$3.GND_8, U$4.GND
MOT_PINCE+: DRIVER_PINCE.10 (3A), U1.9 (LED3)
MOT_PINCE-: DRIVER_PINCE.15 (4A), U1.8 (LED2)
MOT_TREUIL+: DRIVER_PINCE.7 (2A), U1.7 (LED1)
MOT_TREUIL-: DRIVER_PINCE.2 (1A), U1.6 (LED0)
unnamed: DRIVER_PINCE.3 (1Y), MOT_TREUIL1.5
unnamed: DRIVER_PINCE.14 (4Y), PINCE.1
unnamed: SERVO1.1, U1.10 (LED4)
unnamed: SERVO2.1, U1.11 (LED5)
unnamed: HELICE1.1, U1.12 (LED6)
unnamed: HELICE2.1, U1.13 (LED7)
unnamed: DRIVER_PINCE.11 (3Y), PINCE.2
unnamed: DRIVER_PINCE.6 (2Y), MOT_TREUIL1.6
PWM_DIR1: U$3.GPIO4_GPCKL0
SCL_3V: CON-TF-LUNA.3, R_SCL.1, TP_SCL.TP, U1.26 (SCL), U$1.P$2 (RX/SCL), U$3.GPIO3_SCL
SDA_3V: CON-TF-LUNA.2, R_SDA.1, TP_SDA.TP, U1.27 (SDA), U$1.P$3 (TX/SDA), U$3.GPIO2_SDA
VBAT: C_L293.1, DRIVER_PINCE.8 (VCC2), U$2.P$2 (2_VS+), U$4.V_IN

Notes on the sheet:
PWM par PCCA 9685
Pince et treuil
Capteurs
Alim
Cond
Pin RaspberryPi
pour 5V, R trim =268 Ohm

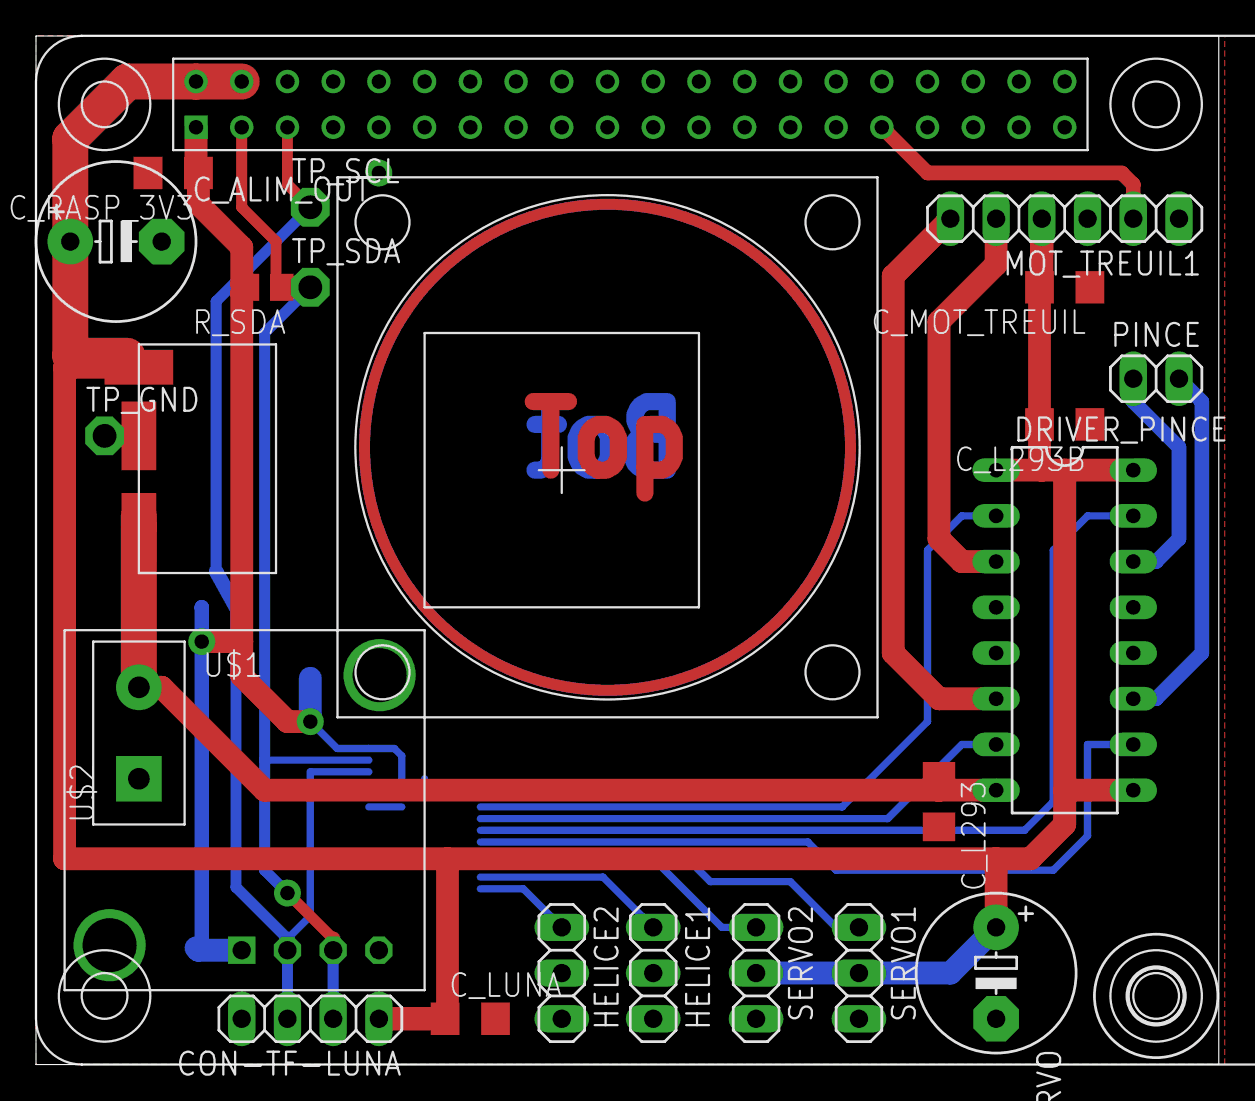
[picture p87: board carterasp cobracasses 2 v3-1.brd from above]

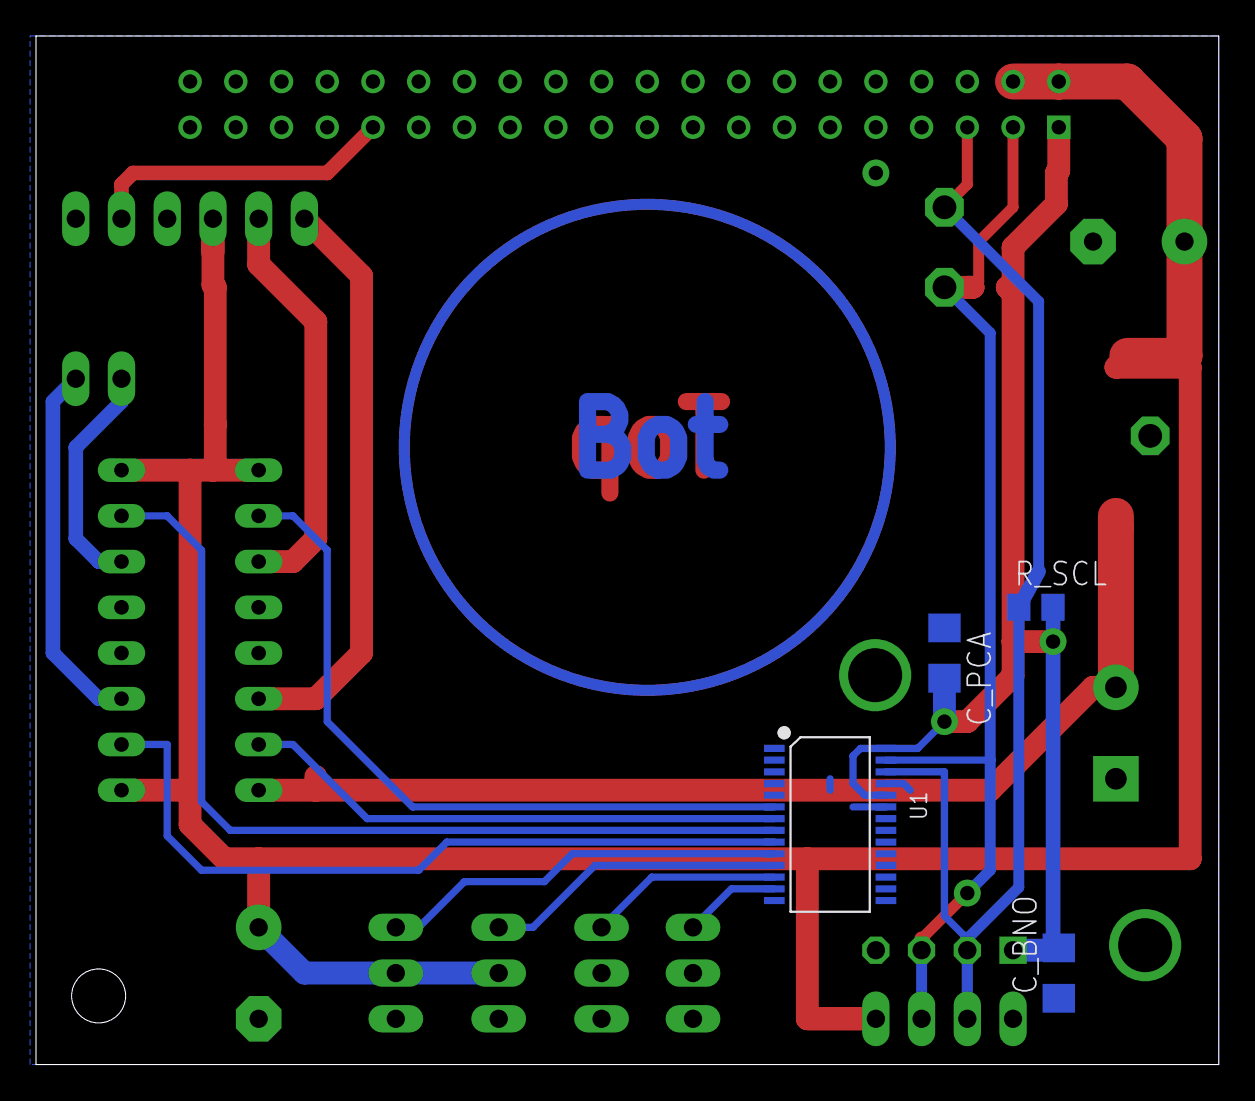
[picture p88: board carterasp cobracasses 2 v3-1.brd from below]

Board: 2 copper layers, 65.7 x 57.1 mm, 29 parts (4 on the bottom side), 19 nets.

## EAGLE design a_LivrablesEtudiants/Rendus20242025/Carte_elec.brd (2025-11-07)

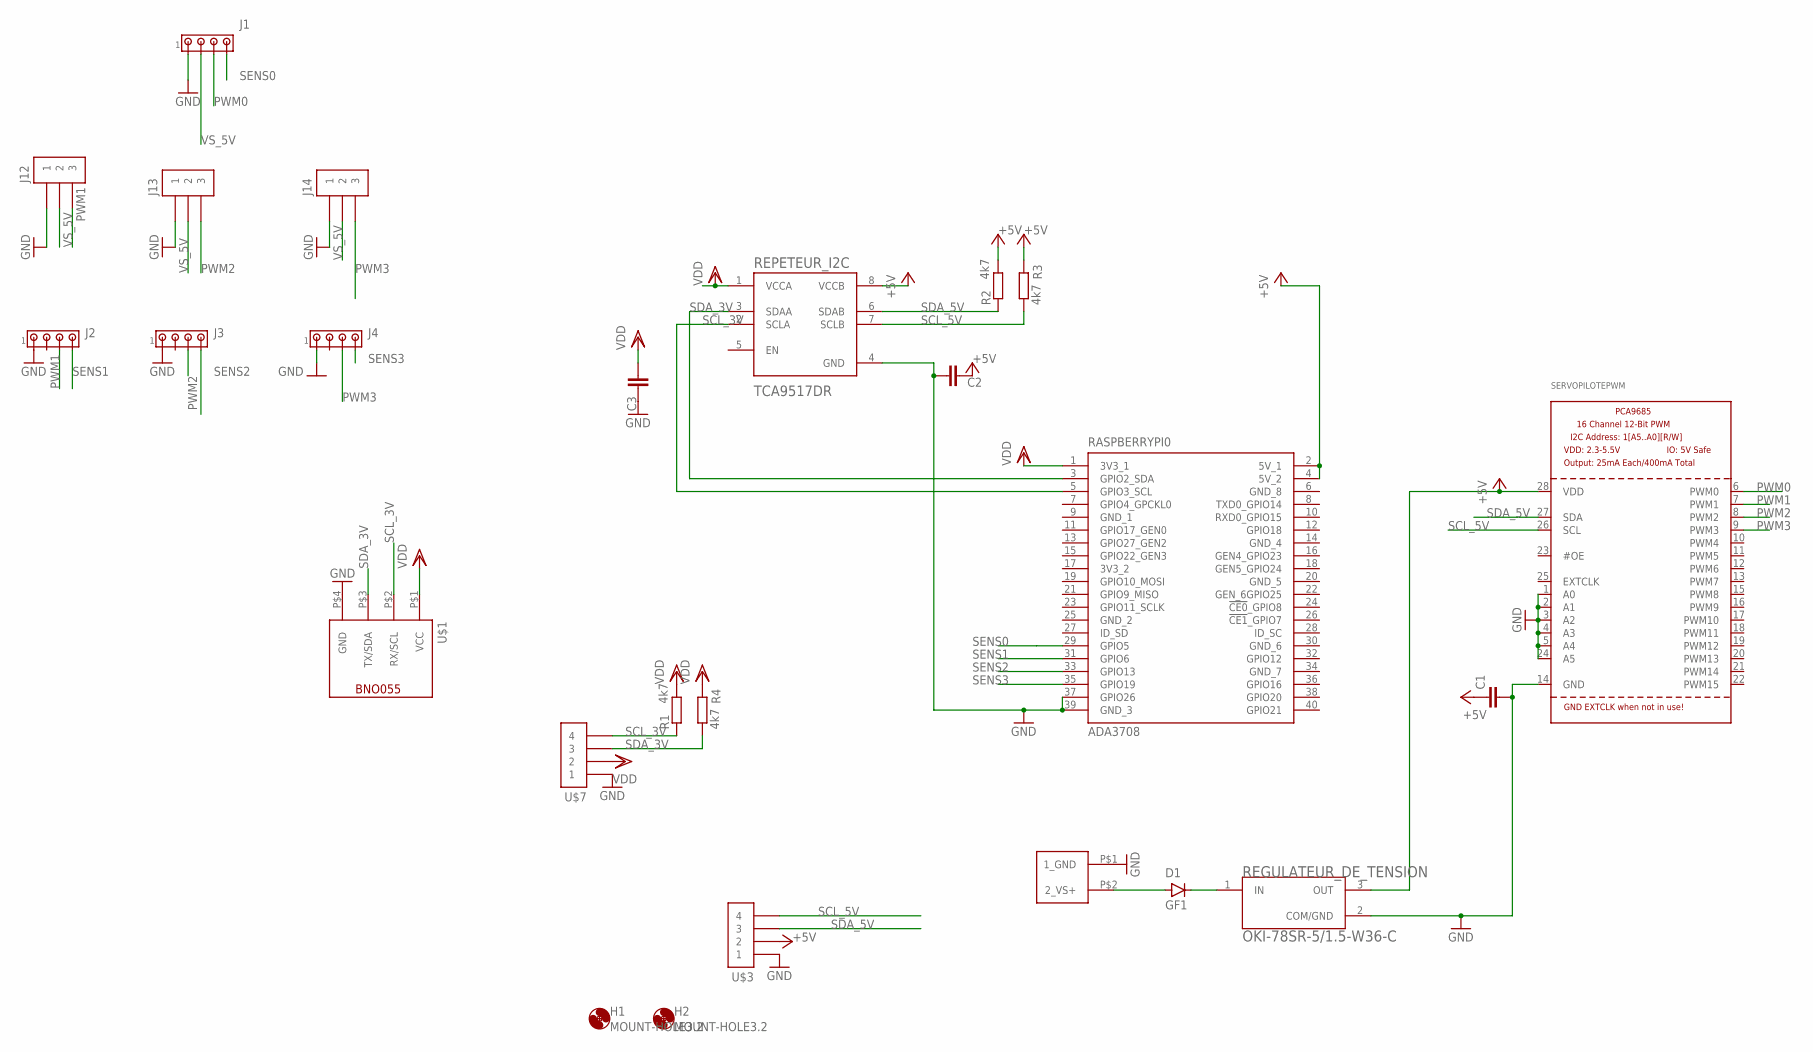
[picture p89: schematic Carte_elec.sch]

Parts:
C1, C2, C3: C-EUC1206; C1206
D1: GF1; SMA-DO214AC
H1, H2: MOUNT-HOLE3.2; 3,2
J1, J2, J3, J4: MTA04-100; 10X04MTA
J12, J13, J14: CAVALIER_3
R1, R2, R3, R4: 4k7; R1206
RASPBERRYPI0: ADA3708; MODULE_ADA3708
REGULATEUR_DE_TENSION: OKI-78SR-5/1.5-W36-C; CONV_OKI-78SR-5/1.5-W36-C
REPETEUR_I2C: TCA9517DR; SOIC127P599X175-8N
SERVOPILOTEPWM: PCA9685; TSSOP28
U$1: MODULE_BNO055
U$2: CONN_ALIM
U$3, U$7: MOLEX_4_DROIT

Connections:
3V3_2: RASPBERRYPI0.17 (3V3_2)
+5V: C1.1, C2.1, R2.2, R3.2, RASPBERRYPI0.2 (5V_1), RASPBERRYPI0.4 (5V_2), REGULATEUR_DE_TENSION.3 (OUT), REPETEUR_I2C.8 (VCCB), SERVOPILOTEPWM.28 (VDD), U$3.P$2 (2)
GND: C1.2, C2.2, C3.1, J1.1, J2.1, J3.1, J4.1, J12.P$1 (1), J13.P$1 (1), J14.P$1 (1), RASPBERRYPI0.37 (GPIO26), RASPBERRYPI0.39 (GND_3), REGULATEUR_DE_TENSION.2 (COM/GND), REPETEUR_I2C.4 (GND), SERVOPILOTEPWM.1 (A0), SERVOPILOTEPWM.2 (A1), SERVOPILOTEPWM.3 (A2), SERVOPILOTEPWM.4 (A3), SERVOPILOTEPWM.5 (A4), SERVOPILOTEPWM.14 (GND), SERVOPILOTEPWM.24 (A5), U$1.P$4 (GND), U$2.P$1 (1_GND), U$3.P$1 (1), U$7.P$1 (1)
GND_1: RASPBERRYPI0.9 (GND_1)
GND_2: RASPBERRYPI0.25 (GND_2)
GND_4: RASPBERRYPI0.14 (GND_4)
GND_5: RASPBERRYPI0.20 (GND_5)
GND_6: RASPBERRYPI0.30 (GND_6)
GND_7: RASPBERRYPI0.34 (GND_7)
GND_8: RASPBERRYPI0.6 (GND_8)
unnamed: D1.A, U$2.P$2 (2_VS+)
unnamed: D1.K (C), REGULATEUR_DE_TENSION.1 (IN)
PWM0: J1.3, SERVOPILOTEPWM.6 (PWM0)
PWM1: J2.3, J12.P$3 (3), SERVOPILOTEPWM.7 (PWM1)
PWM2: J3.3, J13.P$3 (3), SERVOPILOTEPWM.8 (PWM2)
PWM3: J4.3, J14.P$3 (3), SERVOPILOTEPWM.9 (PWM3)
SCL_3V: R1.1, RASPBERRYPI0.5 (GPIO3_SCL), REPETEUR_I2C.2 (SCLA), U$1.P$2 (RX/SCL), U$7.P$4 (4)
SCL_5V: R3.1, REPETEUR_I2C.7 (SCLB), SERVOPILOTEPWM.26 (SCL), U$3.P$4 (4)
SDA_3V: R4.1, RASPBERRYPI0.3 (GPIO2_SDA), REPETEUR_I2C.3 (SDAA), U$1.P$3 (TX/SDA), U$7.P$3 (3)
SDA_5V: R2.1, REPETEUR_I2C.6 (SDAB), SERVOPILOTEPWM.27 (SDA), U$3.P$3 (3)
SENS0: J1.4, RASPBERRYPI0.29 (GPIO5)
SENS1: J2.4, RASPBERRYPI0.31 (GPIO6)
SENS2: J3.4, RASPBERRYPI0.33 (GPIO13)
SENS3: J4.4, RASPBERRYPI0.35 (GPIO19)
VDD: C3.2, R1.2, R4.2, RASPBERRYPI0.1 (3V3_1), REPETEUR_I2C.1 (VCCA), U$1.P$1 (VCC), U$7.P$2 (2)
VS_5V: J1.2, J12.P$2 (2), J14.P$2 (2)

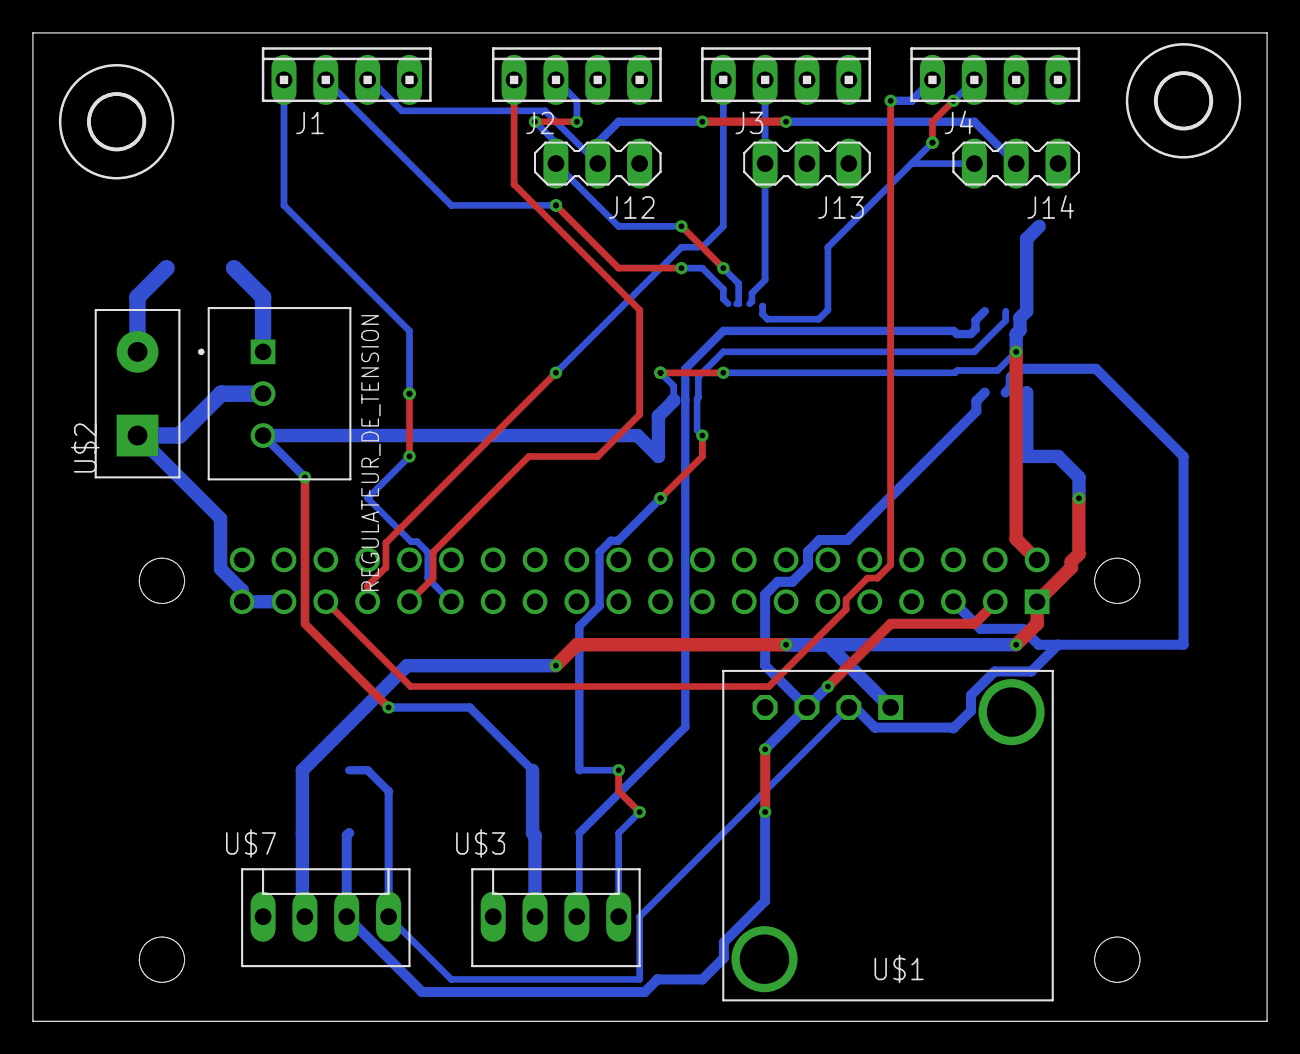
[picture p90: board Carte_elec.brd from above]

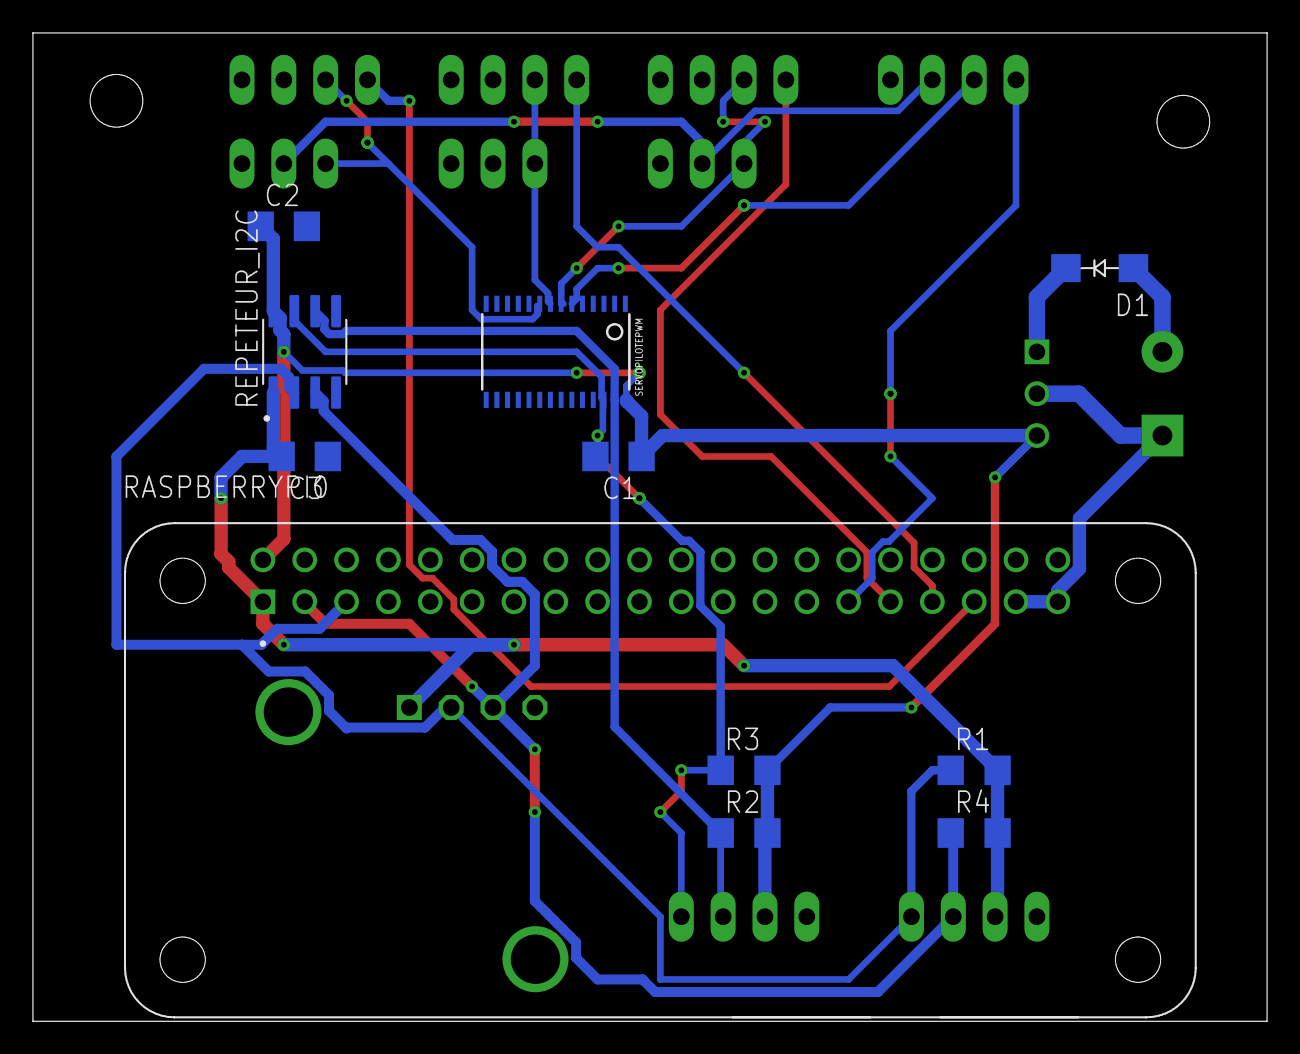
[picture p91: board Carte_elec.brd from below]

Board: 2 copper layers, 74.9 x 60.0 mm, 25 parts (11 on the bottom side), 18 nets.

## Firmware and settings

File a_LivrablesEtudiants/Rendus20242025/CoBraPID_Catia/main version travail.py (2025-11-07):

import rclpy
from rclpy.node import Node
from geometry_msgs.msg import Vector3Stamped
from rclpy.duration import Duration

import time

import time
#from adafruit_servokit import ServoKit #pour utiliser composant PCA9685
#kit = ServoKit(channels=16)
import warnings
from time import sleep
import smbus2
import pygame as p
from pyPS4Controller.controller import Controller
from gpiozero import LED


import threading

class Control(Node):
    def __init__(self):
        super().__init__('control')

        self.CONSIGNE_Z = 2

        Ts = 0.1

        # Altitude control
        P = 20.0
        I = 1.3
        D = 130.0
        N = 0.357

        self.a_alt = [P+D*N, P*N*Ts-2*P+I*Ts-2*D*N, P-P*N*Ts+I*N*Ts*Ts-I*Ts+D*N]
        self.b_alt = [1, N*Ts-2, 1-N*Ts]

        self.err_z = [0,0,0]
        self.commande_z = [0,0,0]

        # Rotation control

        self.pose_received_time = None
        self.pose_timeout = Duration(seconds=0.1)
        self.latest_pose = None
        self.latest_orientation = None

        self.subscription_pose = self.create_subscription(
            Vector3Stamped,
            '/pose_xyz',
            self.pose_callback,
            10  # Hz
        )

        self.subscription_orientation = self.create_subscription(
            Vector3Stamped,
            '/orientation_rpy',
            self.orientation_callback,
            10  # Hz
        )

        self.timer = self.create_timer(0.1, self.timer_callback)  # check every 50 ms

        myi2cbus = smbus2.SMBus(1) # Initialisation du bus I2C
        myPCA9685 = PCA9685(myi2cbus) # Initialisation du générateur de PWM

        numeros_moteurs = {"brushless": [ 1, 2,3, 4], "MCC": [[6, 7], [7, 8]]}

        self.brushless = {}

        self.brushless["d"] = Brushless(myPCA9685,1)
        self.brushless["g"] = Brushless(myPCA9685,2)
        self.brushless["av"] = Brushless(myPCA9685,3)
        self.brushless["ar"] = Brushless(myPCA9685,4)
        self.pince = Pince(myPCA9685, 6)
        self.treuil = Treuil(myPCA9685, 7)

        # Parameters for MyController
        controller_params = {
            "interface": "/dev/input/js0",
            "connecting_using_ds4drv": False,
            "brushless": self.brushless,
            "pince": self.pince,
            "treuil": self.treuil
        }

        # Start a separate thread for the blocking function
        self.controller_thread = threading.Thread(target=self.controller_logic, args=(controller_params,))
        self.controller_thread.start()

        self.get_logger().info("Prêt - Initialisation réalisée")

    def controller_logic(self, controller_params):
        controller = MyController(**controller_params)
        controller.listen()

    def pose_callback(self, msg: Vector3Stamped):
        self.pose_received_time = self.get_clock().now()
        self.latest_pose = msg.vector  # Store the vector
        self.get_logger().debug('Pose received.')

    def orientation_callback(self, msg: Vector3Stamped):
        self.orientation_received_time = self.get_clock().now()
        self.latest_orientation = msg.vector

    def timer_callback(self):
        now = self.get_clock().now()

        if self.pose_received_time is not None and (now - self.pose_received_time) < self.pose_timeout:
            # ✅ Pose is recent (received within the last 0.1 s

            ####### Altitude control #######

            self.get_logger().info(f"Latest Z pose received: {self.latest_pose.z}")

            self.err_z[0] = self.CONSIGNE_Z - self.latest_pose.z

            self.commande_z[0] = self.a_alt[0]*self.err_z[0] + self.a_alt[1]*self.err_z[1] + self.a_alt[2]*self.err_z[2] - self.b_alt[1]*self.commande_z[1] - self.b_alt[2]*self.commande_z[2]

            self.brushless["av"].cmd_vit_pourcent(max(-100, min(self.commande_z[0], 100)))
            self.brushless["ar"].cmd_vit_pourcent(max(-100, min(self.commande_z[0], 100)))

            self.err_z[2] = self.err_z[1]
            self.err_z[1] = self.err_z[0]

            self.commande_z[2] = self.commande_z[1]
            self.commande_z[1] = self.commande_z[0]

        else:
            # ❌ Pose is too old or hasn't been received yet
            self.get_logger().warn('No recent pose.')
            # >>> PLACE YOUR LOGIC HERE (for when pose is stale or missing)
            #self.brushless["d"].cmd_vit_pourcent(0)
            #self.brushless["g"].cmd_vit_pourcent(0)
            self.brushless["av"].cmd_vit_pourcent(0)
            self.brushless["ar"].cmd_vit_pourcent(0)


def main(args=None):
    rclpy.init(args=args)
    node = Control()

    try:
        rclpy.spin(node)
    except KeyboardInterrupt:
        print("\n[INFO] Program interrupted by user (Ctrl+C)")
    finally:
        print("[INFO] Stopping all motors...")

        # Stop all brushless motors
        for key, motor in node.brushless.items():
            motor.stop_mot()
            print(f"[INFO] Motor '{key}' stopped.")

        node.pince.cmd_vit_pourcent(0)
        node.treuil.cmd_vit_pourcent(0)

        node.destroy_node()
        rclpy.shutdown()
        print("[INFO] Shutdown complete.")


if __name__ == '__main__':
    main()

##############################################################################################################################
#################### Classes de controle des moteurs #########################################################################
##############################################################################################################################

class PCA9685:  # pour commander les sorties pwm
    def __init__(self, bus, address_PCA9685=0x40):
        self.available = False
        try:
            # DÉFINITION des registres (valeurs initiales)
            self.address_PCA9685 = address_PCA9685
            self.bus = bus
            self.MODE1 = 0x00  # self.REGISTRE = adresse_registre
            self.MODE2 = 0x01

            # liste de dictionnaires. Chaque dictionnaire definit les registres d'une sortie PWM de la PCA9685
            self.PWMs = [{"ON_L": 0x06, "ON_H": 0x07, "OFF_L": 0x08, "OFF_H": 0x09},
                         {"ON_L": 0x0A, "ON_H": 0x0B, "OFF_L": 0x0C, "OFF_H": 0x0D},
                         {"ON_L": 0x0E, "ON_H": 0x0F, "OFF_L": 0x10, "OFF_H": 0x11},
                         {"ON_L": 0x12, "ON_H": 0x13, "OFF_L": 0x14, "OFF_H": 0x15},
                         {"ON_L": 0x16, "ON_H": 0x17, "OFF_L": 0x18, "OFF_H": 0x19},
                         {"ON_L": 0x1A, "ON_H": 0x1B, "OFF_L": 0x1C, "OFF_H": 0x1D},
                         {"ON_L": 0x1E, "ON_H": 0x1F, "OFF_L": 0x20, "OFF_H": 0x21},
                         {"ON_L": 0x22, "ON_H": 0x23, "OFF_L": 0x24, "OFF_H": 0x25},
                         {"ON_L": 0x26, "ON_H": 0x27, "OFF_L": 0x28, "OFF_H": 0x29}]

            self.PRE_SCALE = 0xFE  # Numero du registre qui code la periode
            self.freqPWM_Hz = 50  # Frequence des PWM
            self.periodPWM = 1 / self.freqPWM_Hz  # 20 millisecondes
            # self.PCA9685_PRE_SCALE_VALUE = (round(25*10**6/(4096*self.freqPWM_Hz)-1)) #32  # configure la fréquence de la PWM sur tous les canaux
            self.PCA9685_PRE_SCALE_VALUE = 125

            # CONFIGURATION des registres du PCA9685
            self.bus.write_byte_data(self.address_PCA9685, self.MODE1, 0x10)
            self.bus.write_byte_data(self.address_PCA9685, self.PRE_SCALE, self.PCA9685_PRE_SCALE_VALUE)
            self.bus.write_byte_data(self.address_PCA9685, self.MODE1, 0x00)
            self.bus.write_byte_data(self.address_PCA9685, self.MODE2, 0x04)

            # Intervalles d’allumage et d’extinction (largeur d'impulsion) pour chaque PWM de self.PWMs.
            for PWM in self.PWMs:
                self.bus.write_byte_data(self.address_PCA9685, PWM["ON_L"], 0)
                self.bus.write_byte_data(self.address_PCA9685, PWM["ON_H"], 0x0)
                self.bus.write_byte_data(self.address_PCA9685, PWM["OFF_L"], 0x40)
                self.bus.write_byte_data(self.address_PCA9685, PWM["OFF_H"], 1)

            self.available = True

        except OSError as e:
            print(f"[ERROR] I2C communication error during PCA9685 initialization: {e}")
            self.available = False

    def commande_moteur_vitesse_us(self, temps_off_us, num_PWM):
        if not self.available:
            print("[WARNING] PCA9685 device not available. commande_moteur_vitesse_us ignored.")
            return
        points_off = temps_off_us * 4095 / (self.periodPWM * 1e6)
        temps_H = int(points_off // 256)
        temps_L = int(points_off % 256)
        try:
            self.bus.write_byte_data(self.address_PCA9685, self.PWMs[num_PWM]["OFF_L"], temps_L)
            self.bus.write_byte_data(self.address_PCA9685, self.PWMs[num_PWM]["OFF_H"], temps_H)
        except OSError as e:
            print(f"[ERROR] I2C communication error during commande_moteur_vitesse_us: {e}")


class Brushless:
    # PCA9685    : instance de la classe PCA9685 utilisee
    # num_moteur : numero de la PWM de la PCA9685
    def __init__(self, PCA9685, num_moteur):
        self.num_moteur = num_moteur
        self.myPCA9685 = PCA9685
        self.valeur_repos = 1500  # valeur milieu de la commande => vitesse nulle
        self.cmd_vit_pourcent(0)

    def stop_mot(self):
        if not self.myPCA9685.available:
            print("[WARNING] PCA9685 device not available. stop_mot ignored.")
            return
        self.myPCA9685.commande_moteur_vitesse_us(0, self.num_moteur)

    def cmd_vit_pourcent(self, vitesse_pourcent):
        if not self.myPCA9685.available:
            print("[WARNING] PCA9685 device not available. cmd_vit_pourcent ignored.")
            return

        if vitesse_pourcent < -100:
            vitesse_pourcent = -100
        if vitesse_pourcent > 100:
            vitesse_pourcent = 100
        if 0 < vitesse_pourcent < 9:
            vitesse_pourcent = 4.5 + vitesse_pourcent / 2
        if 0 > vitesse_pourcent > -9:
            vitesse_pourcent = -4.5 + vitesse_pourcent / 2

        temps_etat_haut_us = self.valeur_repos + vitesse_pourcent * 5
        try:
            self.myPCA9685.commande_moteur_vitesse_us(temps_etat_haut_us, self.num_moteur)
        except OSError as e:
            print(f"[ERROR] I2C communication error in brushless cmd_vit_pourcent: {e}")


class Treuil:
    # PCA9685    : instance de la classe PCA9685 utilisee
    # num_PWM    : numero de la PWM de la PCA9685 connectee a la modulation de vitesse

    def __init__(self, PCA9685, num_PWM):
        self.num_PWM = num_PWM
        self.myPCA9685 = PCA9685
        self.P_horaire = LED(24)
        self.P_antihoraire = LED(23)
        self.cmd_vit_pourcent(0)
    
    def stop(self):
        self.myPCA9685.commande_moteur_vitesse_us(0,self.num_PWM)
        self.P_horaire.off()
        self.P_antihoraire.off()

    def cmd_vit_pourcent(self, vitesse_pourcent):
        if vitesse_pourcent >= 0:
            if vitesse_pourcent > 100:
                vitesse_pourcent = 100
            self.P_horaire.on()
            self.P_antihoraire.off()
            temps_etat_haut_us=200*vitesse_pourcent
            self.myPCA9685.commande_moteur_vitesse_us(temps_etat_haut_us,self.num_PWM)
        else:
            if vitesse_pourcent < -100:
                vitesse_pourcent = -100
            self.P_horaire.off()
            self.P_antihoraire.on()
            temps_etat_haut_us=-200*vitesse_pourcent
            self.myPCA9685.commande_moteur_vitesse_us(temps_etat_haut_us,self.num_PWM)
            
    def kill(self):
        self.P_horaire.close()
        self.P_antihoraire.close()

class Pince:
    # PCA9685    : instance de la classe PCA9685 utilisee
    # num_PWM    : numero de la PWM de la PCA9685 connectee a la modulation de vitesse

    def __init__(self, PCA9685, num_PWM):
        self.num_PWM = num_PWM
        self.myPCA9685 = PCA9685
        self.T_horaire = LED(8)
        self.T_antihoraire = LED(7)
        self.cmd_vit_pourcent(0)

    def stop(self):
        self.myPCA9685.commande_moteur_vitesse_us(0,self.num_PWM)
        self.T_horaire.off()
        self.T_antihoraire.off()
    
    def cmd_vit_pourcent(self, vitesse_pourcent):
        if vitesse_pourcent >= 0:
            if vitesse_pourcent > 100:
                vitesse_pourcent = 100
            self.T_horaire.on()
            self.T_antihoraire.off()
            temps_etat_haut_us=200*vitesse_pourcent
            self.myPCA9685.commande_moteur_vitesse_us(temps_etat_haut_us,self.num_PWM)
        else:
            if vitesse_pourcent < -100:
                vitesse_pourcent = -100
            self.T_horaire.off()
            self.T_antihoraire.on()
            temps_etat_haut_us=-200*vitesse_pourcent
            self.myPCA9685.commande_moteur_vitesse_us(temps_etat_haut_us,self.num_PWM)
    
    def kill(self):
        self.T_horaire.close()
        self.T_antihoraire.close()


##############################################################################################################################
#################### Classe de controle de la mannette #######################################################################
##############################################################################################################################


class MyController(Controller):
    def __init__(self, **kwargs):
        # Extract the parameters for the parent Controller class
        controller_kwargs = {
            'interface': kwargs.get('interface', '/dev/input/js0'),
            'connecting_using_ds4drv': kwargs.get('connecting_using_ds4drv', False)
        }

        # Initialize the parent Controller class with only the expected arguments
        super().__init__(**controller_kwargs)

        # Store additional parameters as instance variables
        self.brushless = kwargs.get('brushless', {})
        self.treuil = kwargs.get('treuil', {})
        self.pince = kwargs.get('pince', {})
        self.vitesse_moy = 0
        self.vitesse_diff = 0
        self.arrêt = True


        # Attributs d'état 
        self.state = {
            'L1': 0,
            'R1': 0,
            'L2': 0, 
            'R2': 0,
            'L3_x': 0,
            'L3_y': 0,
            'R3_x': 0,
            'R3_y': 0,
            'X': 0, # attention c'est un X majuscule !
            'circle': 0,  
            'triangle': 0,
            'square': 0,
            'up_arrow': 0,
            'down_arrow': 0,
            'left_arrow': 0,
            'right_arrow': 0
        }
        
    def on_L2_press(self, value): #avancer
        self.state['L2'] = value

        if not self.arrêt :
            if value<0 :
                value = 0
            value = value*5/3200
            if value >50 :
                value = 50

            if value != 0 :
                print("La valeur de L2 est: ",value)

            self.vitesse_moy = value
            self.brushless["g"].cmd_vit_pourcent(self.vitesse_moy-self.vitesse_diff)
            self.brushless["d"].cmd_vit_pourcent(self.vitesse_moy+self.vitesse_diff)
        
    def on_R2_press(self,value): # reculer
        self.state['R2'] = value

        if not self.arrêt :
            if value<0 :
                value = 0
            value = value*5/3200
            if value >50 :
                value = 50

            if value != 0 :
                print("La valeur de R2 est: ",value)

            self.vitesse_moy = -value
            self.brushless["g"].cmd_vit_pourcent(self.vitesse_moy-self.vitesse_diff)
            self.brushless["d"].cmd_vit_pourcent(self.vitesse_moy+self.vitesse_diff)
    
    def on_R2_release(self):
        self.state['R2'] = 0
    def on_L2_release(self):
        self.state['L2'] = 0
 
    def on_L3_x_at_rest(self):
        self.state['L3_x'] = 0
        #print("L3 au milieu")
        
    def on_R1_press(self):
        self.state['R1'] = 1
        
    def on_R1_release(self):
        self.state['R1'] = 0
    
    def on_L3_right(self,value): #tourner à droite
        self.state['L3_x'] = value

        if not self.arrêt :
            if value<3200 :
                value = 0
            value = value*5/3200
            if value >50 :
                value = 50

            if value != 0 :
                print("L3 droite up value ="+str(value))

            self.vitesse_diff = value
            self.brushless["g"].cmd_vit_pourcent(self.vitesse_moy-self.vitesse_diff)
            self.brushless["d"].cmd_vit_pourcent(self.vitesse_moy+self.vitesse_diff)

    def on_L3_left(self,value): #tourner à gauche
        self.state['L3_x'] = -value

        if not self.arrêt :
            if value>-3200 :
                value = 0
            value = value*5/3200
            if value <-50 :
                value = -50
            
            if value != 0 :
                print("L3 gauche up value ="+str(value))

            self.vitesse_diff = value
            self.brushless["g"].cmd_vit_pourcent(self.vitesse_moy-self.vitesse_diff)
            self.brushless["d"].cmd_vit_pourcent(self.vitesse_moy+self.vitesse_diff)

    def on_L3_up(self,value): 
        self.state['L3_y'] = value
    def on_L3_down(self,value): 
        self.state['L3_y'] = -value

    def on_R3_up(self,value): # monter 
        self.state['R3_y'] = value

        if not self.arrêt :
            if value>-3200 :
                value = 0
            value = value*10/3200
            if value <-100 :
                value = -100
            
            if value != 0 :
                print("R3 up value ="+str(value))
            
            # self.brushless["av"].cmd_vit_pourcent(value)
            # self.brushless["ar"].cmd_vit_pourcent(value)
    
    def on_R3_down(self,value): # descendre
        self.state['R3_y'] = -value

        if not self.arrêt :
            if value<3200 :
                value = 0
            value = value*10/3200
            if value >100 :
                value = 100

            if value != 0 :
                print("R3 down value ="+str(value))
            
            # self.brushless["av"].cmd_vit_pourcent(value)
            # self.brushless["ar"].cmd_vit_pourcent(value)
        
        
    
        
        
    def on_x_press(self):
        self.state['X'] = 1

        self.brushless['ar'].stop_mot()
        self.brushless['av'].stop_mot()
        self.brushless['g'].stop_mot()
        self.brushless['d'].stop_mot()
        self.pince.cmd_vit_pourcent(0)
        self.pince.cmd_vit_pourcent(0)

        self.arrêt = True
        print(self.arrêt)
        
    def on_circle_press(self):
        self.state['circle'] = 1

        #self.brushless["ar"].cmd_vit_pourcent(0)
        #self.brushless["av"].cmd_vit_pourcent(0)
        self.brushless["g"].cmd_vit_pourcent(0)
        self.brushless["d"].cmd_vit_pourcent(0)
        self.arrêt = False
        print(self.arrêt)

    def on_triangle_press(self):
        self.state['triangle'] = 1
    def on_triangle_release(self):
        self.state['triangle'] = 0
    def on_R3_x_at_rest(self):
        self.state['R3_x'] = 0

    def on_R3_right(self,value):
        self.state['R3_x'] = value

    def on_R3_left(self,value):
        self.state['R3_x'] = -value

    def on_L3_up(self,value):
        self.state['L3_y'] = value

    def on_L3_down(self,value):
        self.state['L3_y'] = -value

    def on_circle_release(self):
        self.state['circle'] = 0

    def on_L1_press(self):
        self.state['L1'] = 1

    def on_L1_release(self):
        self.state['L1'] = 0

    def on_x_release(self):
        self.state['X'] = 0

    def on_L3_y_at_rest(self):
        self.state['L3_y'] = 0
        self.vitesse_diff = 0

    def on_R3_y_at_rest(self):
        self.state['R3_y'] = 0



    # ------------
    # PARTIE ENZO
    # ------------

    # TREUIL
    def on_square_press(self):
        self.state['square'] = 1

        if self.sens_treuil == "bas" :
            while self.contact == True :
                self.treuil.cmd_vit_pourcent(-100)
            while self.contact == False :
                self.treuil.cmd_vit_pourcent(-100)
            self.sens_treuil = "haut"
        elif self.sens_treuil == "haut" :
            while self.contact == True :
                self.treuil.cmd_vit_pourcent(100)
            while self.contact == False :
                self.treuil.cmd_vit_pourcent(100)
            self.sens_treuil = "bas"
        else :  
            pass


    def on_up_arrow_press(self):
        self.state['up_arrow'] = 1

        #brushless["t"].cmd_vit_pourcent(50)
        print("Montée treuil")
        if not self.arrêt:
            self.treuil.cmd_vit_pourcent(100)
            pass
            

    def on_down_arrow_press(self):
        self.state['down_arrow'] = 1

        #brushless["t"].cmd_vit_pourcent(-50)
        print("Descente treuil")
        if not self.arrêt:
            self.treuil.cmd_vit_pourcent(-100)
            pass

    
    def on_up_down_arrow_release(self):
        self.state['up_arrow'] = 0
        self.state['down_arrow'] = 0

        self.treuil.cmd_vit_pourcent(0)
        print("Arrêt treuil")

    # PINCE
    def on_right_arrow_press(self):
        self.state['right_arrow'] = 1

        if not self.arrêt:
            self.pince.cmd_vit_pourcent(100)
            print("Fermeture pince")

    def on_left_arrow_press(self):
        self.state['left_arrow'] = 1

        if not self.arrêt:
            self.pince.cmd_vit_pourcent(-100)
            print("Ouverture pince")
    
    def on_left_right_arrow_release(self):
        self.state['right_arrow'] = 0
        self.state['left_arrow'] = 0

        self.pince.cmd_vit_pourcent(0)
        print("Arrêt pince")

#La bibliothèque que nous avons écrite se base sur la bibliothèque adafruit_servokit

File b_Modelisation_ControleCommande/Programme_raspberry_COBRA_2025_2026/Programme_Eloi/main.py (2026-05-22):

import time
import tf_luna   # lidar
from math import *
from PID import *
from centrale_inirtielle import *
from serveur import *
import localisation_2026
import listes_points
import deplacement
from position_cam_fix import PosCamFix


myi2cbus = smbus2.SMBus(1) # Initialisation du bus I2C


dep = deplacement.Deplacement(myi2cbus)
lidar = tf_luna.LidarTFLuna(myi2cbus)
loc = localisation_2026.LocalisationRuning(listes_points.liste_atrium, 5)

etat = -1
list_pos_cons = [(1, 1, 1), (5, 1, 2), (1, 5, 3)]

dt_etat = 0

serveur = Serveur(donnee, mes_donnee)
serveur.start()


PID_alt = PID(40, 0, 400, 40, 50, 0.05)
PID_lacet = PID(1, 0, 5, 40, 50, 0.1)

PID_x = PID(15, 0.0, 0, 20, 50, 1)
PID_y = PID(15, 0.0, 0, 20, 50, 1)

PID_alt.etat = False
PID_lacet.etat = False
PID_x.etat = False
PID_y.etat = False


stab_time = 5

lacet_consigne = 0

donnee["amp"] = 30
donnee["alt"] = PID_alt.consigne
donnee["angle"] = lacet_consigne
donnee["x"] = PID_x.consigne
donnee["y"] = PID_y.consigne
donnee["PID_alt"] = PID_alt.sendPIDJson()
donnee["PID_angle"] = PID_lacet.sendPIDJson()
donnee["PID_pos"] = PID_x.sendPIDJson()


loc_cam_fix = PosCamFix()
loc_cam_fix.start()



loc.Start()
i = 0
old_t = time.time()
runing = True
try:
    while runing:
        t = time.time()
        dt = t - old_t
        old_t = t

        if serveur.new_data:
            serveur.new_data = False
            PID_alt.consigne = donnee["alt"]
            lacet_consigne = donnee["angle"]
            
            PID_alt.loadPIDJson(donnee["PID_alt"])
            PID_lacet.loadPIDJson(donnee["PID_angle"])
            PID_x.loadPIDJson(donnee["PID_pos"])
            PID_y.loadPIDJson(donnee["PID_pos"])
            print(serveur.new_data_type)
            

            if donnee["etas_pos"]:
                etat = 0
            else:
                etat = -1
                PID_alt.etat = donnee["etas_alt"]
                PID_lacet.etat = donnee["etas_angle"]
                PID_x.etat = False
                PID_y.etat = False
                

            if "x" in serveur.new_data_type and "y" in serveur.new_data_type:
                list_pos_cons.append((donnee["x"], donnee["y"], donnee["alt"]))

            serveur.new_data_type = []

        
        if loc.new_data or True:
            loc.new_data = False

            tangage, roulis, lacet_ = Centrale.read_euler()

            lacet = (360 - loc.lacet - 90) % 360


            d = lidar.mesure_distance()
            alt = d*cos(tangage*pi/180)*cos(roulis*pi/180)



            relative_lacet = (lacet - (lacet_consigne % 360) + 180) % 360 - 180


            purcent_lacet = PID_lacet.update(relative_lacet, dt)
            purcent_alt = PID_alt.update(alt, dt)

            if len(list_pos_cons) > 0:
                x1, y1 = loc.Rtags_to_Rcobra(list_pos_cons[0][0], list_pos_cons[0][1])
                purcent_x = PID_x.update(x1, dt)
                purcent_y = PID_y.update(y1, dt)


            if donnee["c"] == "0":
                dep.setAltitude(purcent_alt + donnee["offset_alt"] * PID_alt.etat)
                dep.setAngle(-purcent_lacet)
                dep.setX(-purcent_x)
                dep.setY(purcent_y)


            mes_donnee["alt"] = alt
            mes_donnee["angle"] = relative_lacet

            mes_donnee["alt_cons"] = PID_alt.consigne
            mes_donnee["angle_cons"] = lacet_consigne % 360

            mes_donnee["alt_force"] = purcent_alt
            mes_donnee["angle_force"] = purcent_lacet
            
            mes_donnee["x"] = loc.x0
            mes_donnee["y"] = loc.y0
            mes_donnee["x_fix"] = loc_cam_fix.x0
            mes_donnee["y_fix"] = loc_cam_fix.y0
            mes_donnee["angle_fix"] = loc_cam_fix.theta
            serveur.new_donnee = True

            erreur = ((loc.x0 - loc_cam_fix.x0)**2 + (loc.y0 - loc_cam_fix.y0)**2)**0.5

            i += 1
            if (i % 50) == 0 and len(list_pos_cons) > 0:
                print(f"i:{i}\t erreur:{round(erreur, 3)}\t etat: {etat}\tx0: {loc.x0:.2f}\ty0: {loc.y0:.2f}\tlacet: {lacet:.2f} \tlacet_cons: {lacet_consigne:.2f}\trelative_lacet: {relative_lacet:.2f}\tx1: {x1:.2f}\ty1: {y1:.2f}")




        match etat:
            case 0:
                if len(list_pos_cons) > 0:
                    etat = 1

                    PID_x.etat = False
                    PID_y.etat = False


                    PID_alt.consigne = list_pos_cons[0][2]
                    PID_alt.etat = True
                    dt_etat = time.time()

            case 1:
                
                if abs(alt-PID_alt.consigne) < 0.1:             # si la consigne en altutide est respectee
                    if dt_etat + stab_time < time.time():
                        etat = 2

                        Dx = list_pos_cons[0][0] - loc.x0
                        Dy = list_pos_cons[0][1] - loc.y0

                        lacet_consigne = (atan2(Dy, Dx) * 180/pi) % 360

                        del list_pos_cons[0]
                        
                        PID_lacet.etat = True
                        dt_etat = time.time()
                else:
                    dt_etat = time.time()
            case 2:
                
                if abs(relative_lacet) < 20:                # si la consigne en angle est respectee
                    if dt_etat + stab_time < time.time():
                        etat = 3
                        PID_x.etat = True
                        PID_y.etat = True
                        dt_etat = time.time()
                else:
                    dt_etat = time.time()
            
            case 3:
                x1, y1 = loc.Rtags_to_Rcobra(list_pos_cons[0][0], list_pos_cons[0][1])
                if (x1**2 + y1**2)**0.5 < 1:
                    
                    if dt_etat + stab_time < time.time():                    # si les consignes en position sont respectes
                        if len(list_pos_cons) > 0:
                            etat = 0
                        else:
                            etat = 4
        
                else:
                    dt_etat = time.time()
                    
            case 4:
                if len(list_pos_cons) > 0:
                    etat = 0


            case -1:
                pass


        if donnee["c"]:
            amp = donnee["amp"]

            match donnee["c"]:

                case "z":
                    dep.setX(amp)
                
                case "s":
                    dep.setX(-amp)
                
                case "q":
                    dep.setY(-amp)
                
                case "d":
                    dep.setY(amp)
                
                case "a":
                    dep.setAngle(-amp)
                
                case "e":
                    dep.setAngle(amp)
                
                case "Shift_L":
                    dep.setAltitude(amp)
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

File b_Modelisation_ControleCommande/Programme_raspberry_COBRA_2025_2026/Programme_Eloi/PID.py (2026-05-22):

import filtres_2025 as filtre

# Kp : gain P
# Ki : gain I
# Kd : gain D
# sat : saturation (dans notre cas c'est 100)
# sample_time : ecart de temps entre chaque update de l'asservicement (environ 0.02 et 0.1)



class PID:
    def __init__(self, Kp, Ki, Kd, sat, sample_time, fc):
        self.Kp, self.Ki, self.Kd, self.sat, self.sample_time = Kp, Ki, Kd, sat, sample_time
        
        self.ret = 0            # valeur retourné par le block asservicement
        self.consigne = 0       # conssigne
        self.sum = 0            # intégrale
        self.old_erreur = None     # utilisé pour la dérivée

        self.dt_update = 0      # delta T entre chaque execution de l'asservicement
        self.derive_filtre = 0  # filtre pass-bas pour filtrer la dérivée

        self.Corr_Kp, self.Corr_Ki, self.Corr_Kd = 0, 0, 0
        self.mes = 0
        self.filtre_derive = filtre.PasseBas_ordre_1(fc)

        self.etat = True

    def __str__(self):
        return str(round(self.ret, 3)) + "\t" + \
                str(round(self.Corr_Kp, 3)) + "\t" + \
                str(round(self.Corr_Ki, 3)) + "\t" + \
                str(round(self.Corr_Kd, 3)) + "\t" + \
                str(round(self.mes, 3)) + "\t" + \
                str(round(self.derive_filtre, 3))
        
    def update(self, mes, dt):

        if not self.etat:
            return 0

        self.dt_update += dt
        self.mes = mes
        if self.dt_update < 1.0/self.sample_time:
            return self.ret

        erreur = self.consigne - mes

        self.Corr_Kp = self.Kp * erreur



        self.sum += erreur * self.dt_update
        if self.Ki != 0:
            if self.sum > self.sat/self.Ki: self.sum = self.sat / self.Ki        #  saturation du correcteur i
            elif self.sum < -self.sat/self.Ki: self.sum = -self.sat / self.Ki

        self.Corr_Ki = self.Ki * self.sum

        


        if self.old_erreur == None: self.old_erreur = erreur
        derive = (erreur - self.old_erreur) / self.dt_update
        self.old_erreur = erreur

        self.derive_filtre = self.filtre_derive.filtre1(derive, self.dt_update)    #  filtrage de la dérivée

        

        self.Corr_Kd = self.Kd * self.derive_filtre


        self.ret = self.Corr_Kp + self.Corr_Ki + self.Corr_Kd


        if self.ret > self.sat: self.ret = self.sat    #  saturation de tout les correcteurs
        elif self.ret < -self.sat: self.ret = -self.sat

        self.dt_update = 0
        return self.ret
    

    def loadPIDJson(self, json_data):
        self.Kp = json_data["Kp"]
        self.Ki = json_data["Ki"]
        self.Kd = json_data["Kd"]
        self.sample_time = json_data["sample_time"]
        self.filtre_derive.fc = json_data["filtre_derivee"]
        self.sat = json_data["saturation"]
        print("loadPIDJson: ",self.sat)

        

    def sendPIDJson(self):
        json_data = {}
        json_data["Kp"] = self.Kp
        json_data["Ki"] = self.Ki
        json_data["Kd"] = self.Kd
        json_data["sample_time"] = self.sample_time
        json_data["filtre_derivee"] = self.filtre_derive.fc
        json_data["saturation"] = self.sat
        return json_data

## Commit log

2025-11-07 Deleting history
    [01-Pince_test2_V3.stl, 01-Pince_test_V3.CATPart, 01-Pince_test_V3.stl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]
2025-11-07 ajout des docs constructeur du ballon
2025-11-07 ajout essais asservissement 202506
    [PROP-DATA-FILE_202312.xlsx, Propeller Thrust Calc.xlsx, data_essai_indiciel_2.csv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]
2025-11-07 Revise README for 2025-2026 progress updates
    Updated the README to reflect progress and changes for 2025-2026, including updates on localization solutions and sensor integration.
2025-11-07 Update avancement.md with november 7th
    Clarified the work on 'lacet' with motor direction details.
2025-11-14 Update Readme with project advancements
    Added updates on camera testing and GPS Indoor.
2025-11-19 Ajout de l'article culture sciences de l'ingénieur
2025-11-19 renommage de la partie livrable janvier 2025
2025-11-21 Update avancement.md with PID settings
    Added PID parameters for control in the document.
2025-11-28 Update motor pin assignments and test library
    Updated motor pin assignments and tested library version.
2025-12-01 Ajout des cartes électroniques 2025
    [PCB-CobraPID.brd, PCB-CobraPID.sch, carterasp cobracasses 2 v3-1.brd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]
2026-02-20 Add propeller details to composantsCobra.md
    Added propeller information for the CoBRA dirigible.
2026-02-20 Add price for AS2303 F3P motors
2026-02-20 Add link for AS2303 F3P motor
    Added a link for the AS2303 F3P motor specifications.
2026-02-20 Modify propeller details in composantsCobra.md
    Updated the propeller information with a new price and link.
2026-04-17 Update composantsCobra.md with new components
    Added ESC, LiDAR, accelerometer, and pressure sensor details.
2026-05-22 Update battery link in composantsCobra.md
2026-06-15 Add readme for camera calibration automation
    Added information about automated camera calibration process.
2026-06-15 Update readme2.md for camera calibration details
    Clarified the process of camera calibration and photo capture.

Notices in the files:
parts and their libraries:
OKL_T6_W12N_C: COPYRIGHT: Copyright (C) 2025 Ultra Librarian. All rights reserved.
